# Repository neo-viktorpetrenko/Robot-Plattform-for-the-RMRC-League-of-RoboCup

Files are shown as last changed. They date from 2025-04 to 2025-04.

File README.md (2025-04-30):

# Robot-Plattform-for-the-RMRC-League-of-RoboCup
A Repository for Sharing an easily modifiable and reproducible Robot Plattform including a suspension that was used in the RoboCup German Open 2025 competition

On this Repository a Mechanical Design of a 6 wheeled robot is shared. The robot uses mainly electronic components from EduArt.

cropped

## List of 3D Models
### Models for the front, back and sides of the chassis
|*Amount* | *Component* | *Heatset Inserts M3* | *Multi Filament Print* | *Support Material* | 
| ----- | ----- | ----- | ----- | ----- |
| 1 | Plate Front | 4 | X | X |
|2|Frontlight Cover||✔|X|
|1|Plate Back|4|X|X|
|2|Rearlight Cover||✔|X|
|2|Plate Side A||✔|X|
|1|Plate Side B||✔|X|
|1|Plate Side B with IO Hole||✔|X|

### Models for the floor of the chassis
|*Amount* | *Component* | *Heatset Inserts M3* | *Multi Filament Print* | *Support Material* | 
| ----- | ----- | ----- | ----- | ----- |
|1|Raspberry Pi Bracket||X|X|
|1|Battery Case|4|X|✔|
|1|Plate Bottom A|12 + 4 x M2.5|X|X|
|1|Plate Bottom B|8|X|X|

### Models for the roof of the chassis
|*Amount* | *Component* | *Heatset Inserts M3* | *Multi Filament Print* | *Support Material* | 
| ----- | ----- | ----- | ----- | ----- |
|1|Router Case|4|X|✔|
|1|Plate Top A||X|X|
|1|Plate Top B||X|X|
|1|Plate Top Main Input||X|X|
|1|Camera Servo Holder|4|X|X|
|1|Camera Holder||X|X|

### Models for the suspension
|*Amount* | *Component* | *Heatset Inserts M3* | *Multi Filament Print* | *Support Material* | 
| ----- | ----- | ----- | ----- | ----- |
|4|Suspension Support Center|5|X|X|
|2|Suspension Support Outside|1|X|X|
|6|Suspension Partial Axis|2|X|✔|
|6|Suspension Axis Attachment Plate||X|X|
|3|Suspension Axis Cover||X|X|
|2|Suspension Electronics Cover||X|X|
|3|Motorshield Adapter Plate|2|X|X|
|6|Wheel||✔|✔|

## List of additional components you'll have to buy
| *Amount* | *Component* | *Details* | *Link* |
| ---- | ---- | ---- | ---- |
| 6 | DC Motors | PG25M370 Dc Planetary Gear Motor with Encoder Gear Ratio 64:1 | https://www.nbleisonmotor.com/PG222238-Dc-Planetary-Gear-Motor-pd6514204.html |
| 6 | Torsion Spring | Chosen by calculation, Direction: 90°, used here: Febrotec 0T085-090-422 | https://www.febrotec.de/de-DE/torsionsfedern-schenkelfedern/0t085-090-422/ |
| 1 | Makerbeam Starter Kit |  | https://www.makerbeam.com/makerbeam-makerbeam-regular-starter-kit-black.html |
| 12 | Bearing | Ball Bearing DIN 6002 ZZ 2Z 15x32x9 mm | https://www.conrad.de/de/p/reely-kugellager-radial-chromstahl-innen-durchmesser-15-mm-aussen-durchmesser-32-mm-drehzahl-max-24000-u-min-221954.html |
| 50 cm | Nylon String | diameter 5mm | https://www.conrad.de/de/p/nylonfaden-0-5-mm-100-m-800620811.html |
| 4 | Heat Set Inserts | M2.5x4 | https://www.amazon.de/dp/B09J91JWGM?ref=ppx_yo2ov_dt_b_fed_asin_title&th=1 |
| < 100 | eat Set Inserts | M3x3 | https://www.amazon.de/dp/B09FXNX6WF?ref=ppx_yo2ov_dt_b_fed_asin_title&th=1 |
| 24 | Screws for motors | M2x6 | |
| 4 | Screws for Raspberry Pi 5 | M2.5x10 | |
| 1 | Servo motor for the camera | FT90M Digital Servo  270° Drehwinkel | |
| 6 | Tires | 1:10 RC rubber tires  120 mm outer diameter | https://www.pololu.com/product/1557 |

## Suspension Design
The Suspension of this platform is inspired by the now discontinued Dagu Wild Thumper platform. It uses torsion springs attached to rotating motor enclosures to ensure contact with uneven ground.  Two enclosures on each side are connected with a nylon string to prevent the springs from rotating the enclosures too much.

There are some python scripts in this repository that aid in calculating the behavior of the suspension if you want to modify that. The most relevant dimensions of the suspension are shown in the images below. k in the scripts is the spring constant of the torsion spring. If you order your Springs from Febrotec, you can calculate k = (Max. Torque Md)/(Max. Torsion alpha). For a linear behavior of the suspension, the springs should not be used near the 90-degree rest position. The Most important forces of the calculation are the spring force Ff, the weight Fg and the force acting on a wheel FR.

The Script Suspension_one_curve generates a graph of the force that acts on the wheel at each point in the spring travel xR.
The Script suspension_average_forces generates a grid of the average force within the spring travel for different configurations of l0 and dA1.

CAD2

Zeichnung Drehfeder

Drehfeder rechnung6

grafik

drehfeder rechnung1

grafik

If you don't know the final weight of your modified robot, you can use the excel sheet spring_force_estimation to find out what torsion spring you need. You can set the maximum and minimum weight that your robot will have and change the spring constant to one of a torsion spring you found online. You can use the spring. if the calculated line fits well within the bounds you've set like shown in the graph below.

dimensionierung drehfeder 1

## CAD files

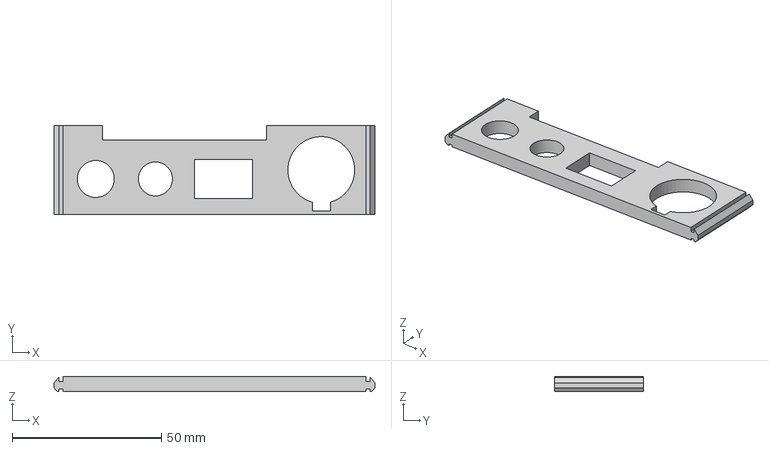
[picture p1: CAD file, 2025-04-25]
Robot Models/Plates/top/Plate Top Main Input/Plate Top Main Input.step
107.6 x 30.0 x 4.89 mm

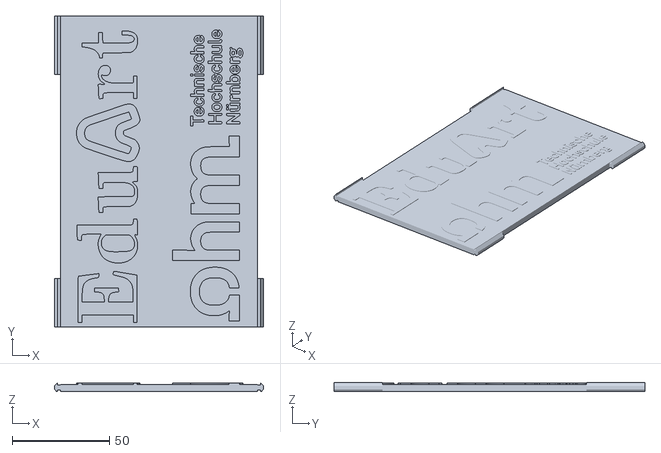
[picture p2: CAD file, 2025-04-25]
Robot Models/Plates/front back sides/Plate Side A/Plate Side A Main Body.stl
107.6 x 160.0 x 4.68

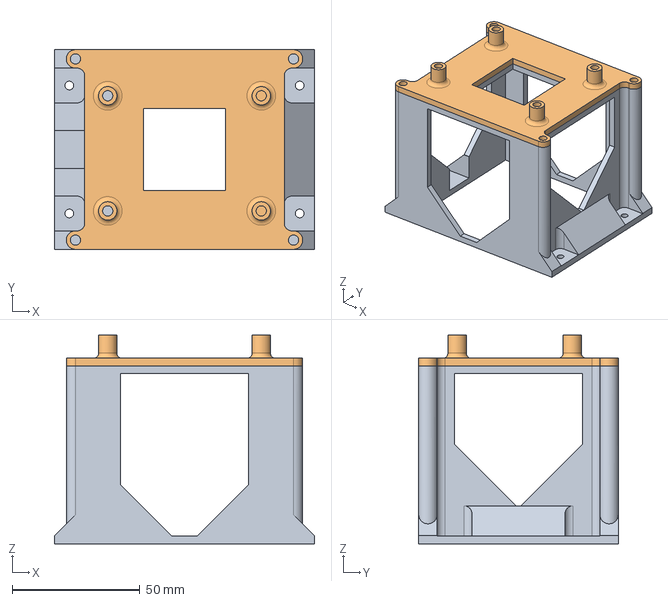
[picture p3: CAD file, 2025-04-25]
Robot Models/Plates/floor/Battery Case/Battery Case.step
101.6 x 78.0 x 81.5 mm

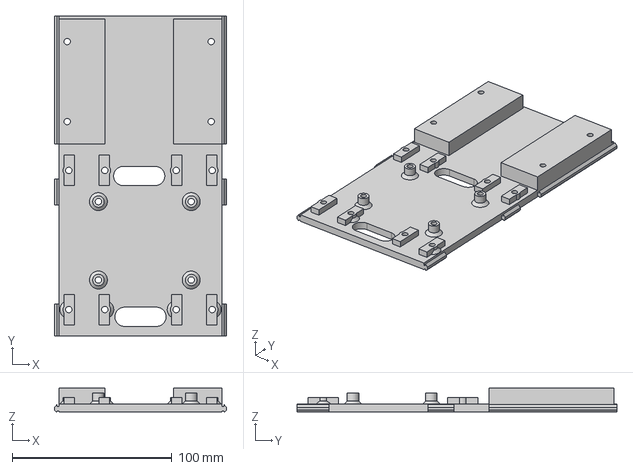
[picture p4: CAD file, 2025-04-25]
Robot Models/Plates/floor/Plate Bottom A/Plate Bottom A.step
107.6 x 200.0 x 14.9 mm

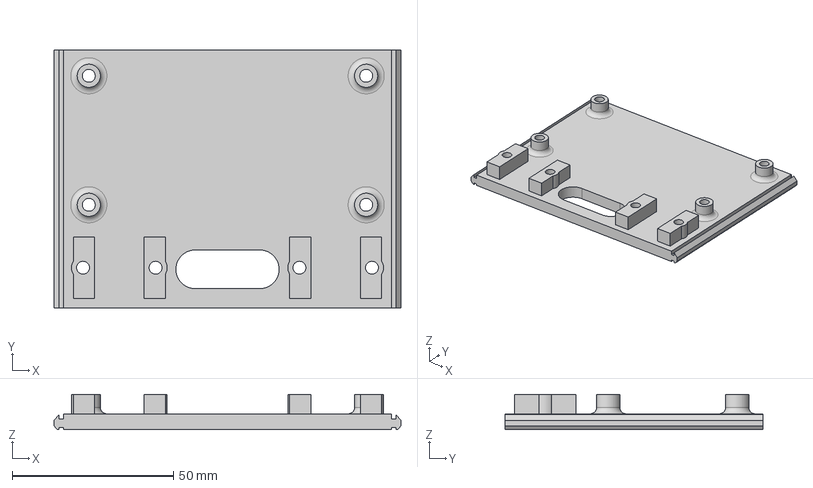
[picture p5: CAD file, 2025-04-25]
Robot Models/Plates/floor/Plate Bottom B/Plate Bottom B.step
107.6 x 80.0 x 10.9 mm

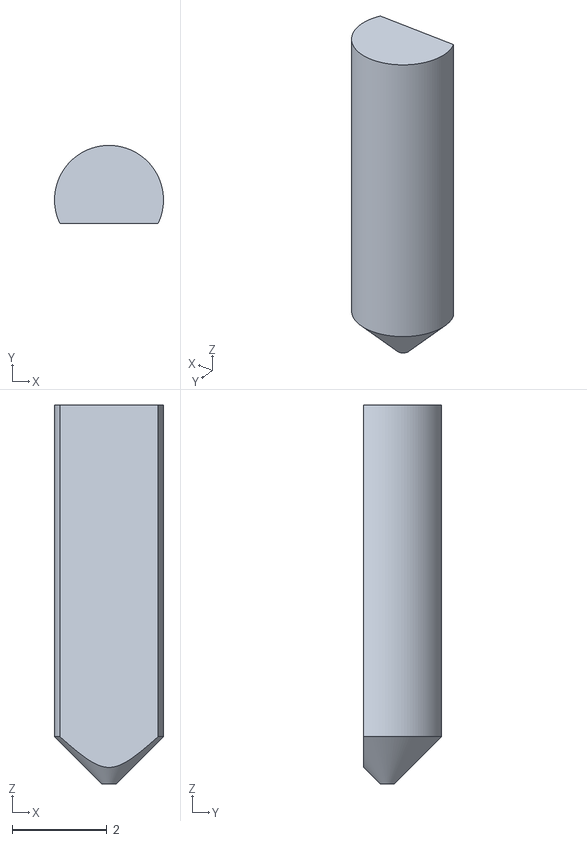
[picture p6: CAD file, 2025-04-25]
Robot Models/Plates/floor/Raspberry PI Bracket/Raspberry PI Bracket pt2.stl
2.30 x 1.65 x 8.00

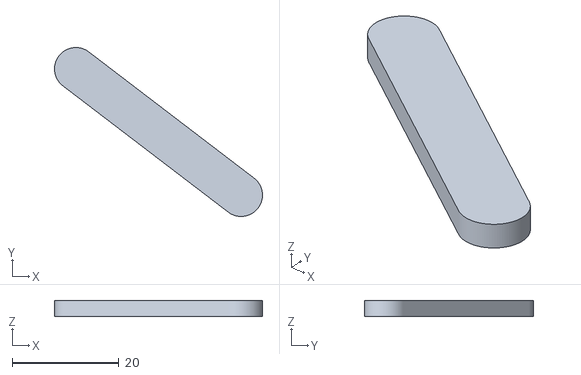
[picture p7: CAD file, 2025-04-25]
Robot Models/Plates/front back sides/Frontlight Cover/Frontlight Cover pt3.stl
39.0 x 31.7 x 3.00

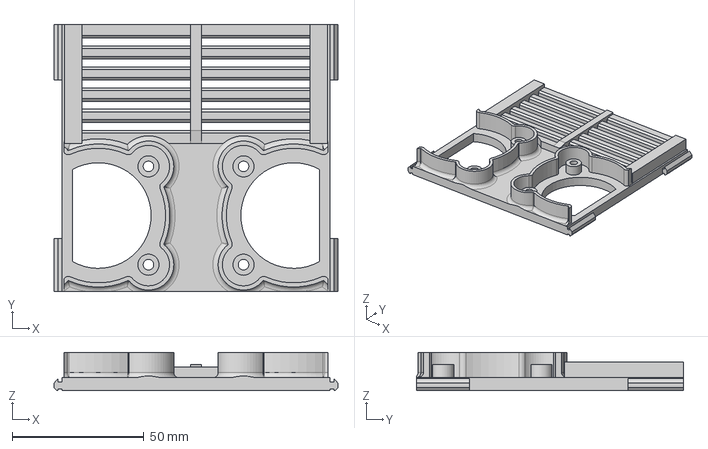
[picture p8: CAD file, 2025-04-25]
Robot Models/Plates/front back sides/Plate Back/Plate Back.step
107.6 x 101.0 x 14.5 mm

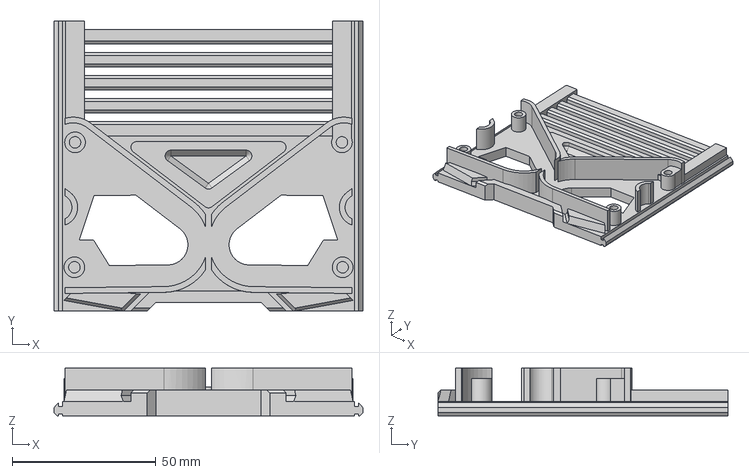
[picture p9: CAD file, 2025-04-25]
Robot Models/Plates/front back sides/Plate Front/Plate Front.step
107.6 x 101.0 x 16.6 mm

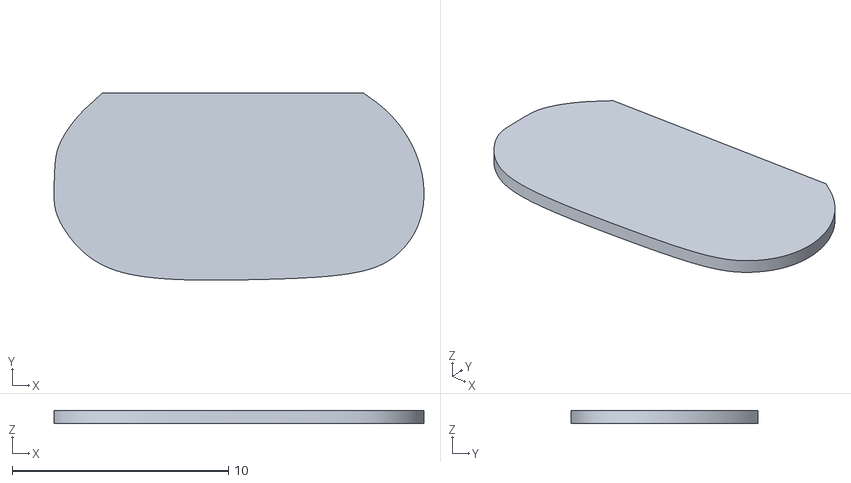
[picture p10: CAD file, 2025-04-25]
Robot Models/Plates/front back sides/Plate Side A/Plate Side A text10.stl
17.1 x 8.67 x 0.6

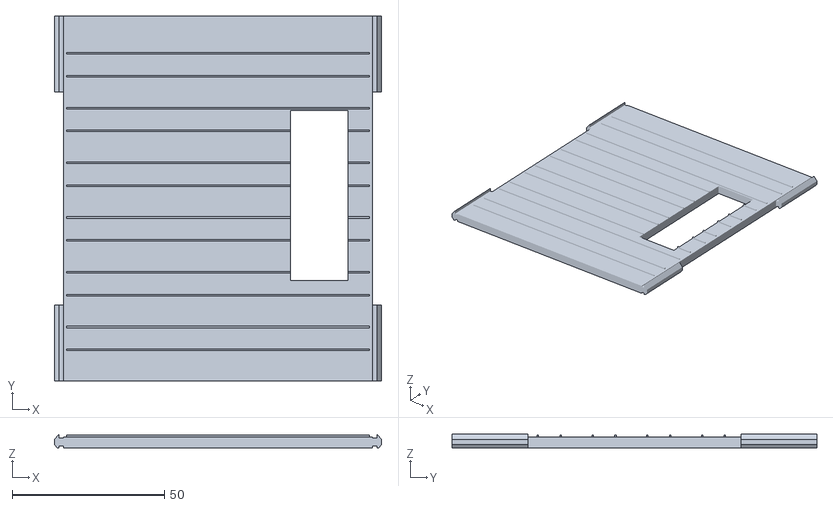
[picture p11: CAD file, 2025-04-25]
Robot Models/Plates/front back sides/Plate Side B with IO Hole/Plate Side B with IO Hole pt1.stl
107.6 x 120.0 x 4.68

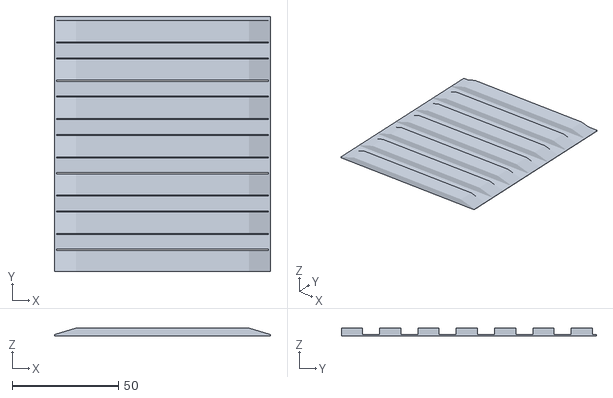
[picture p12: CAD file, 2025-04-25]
Robot Models/Plates/front back sides/Plate Side B/Plate Side B pt2.stl
101.6 x 120.0 x 3.60

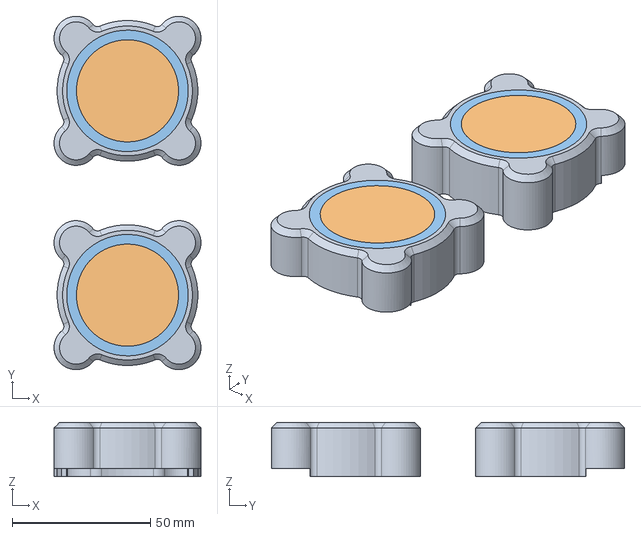
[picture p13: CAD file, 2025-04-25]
Robot Models/Plates/front back sides/Rearlight Cover/Rearlight Cover.step
53.2 x 128.0 x 19.6 mm

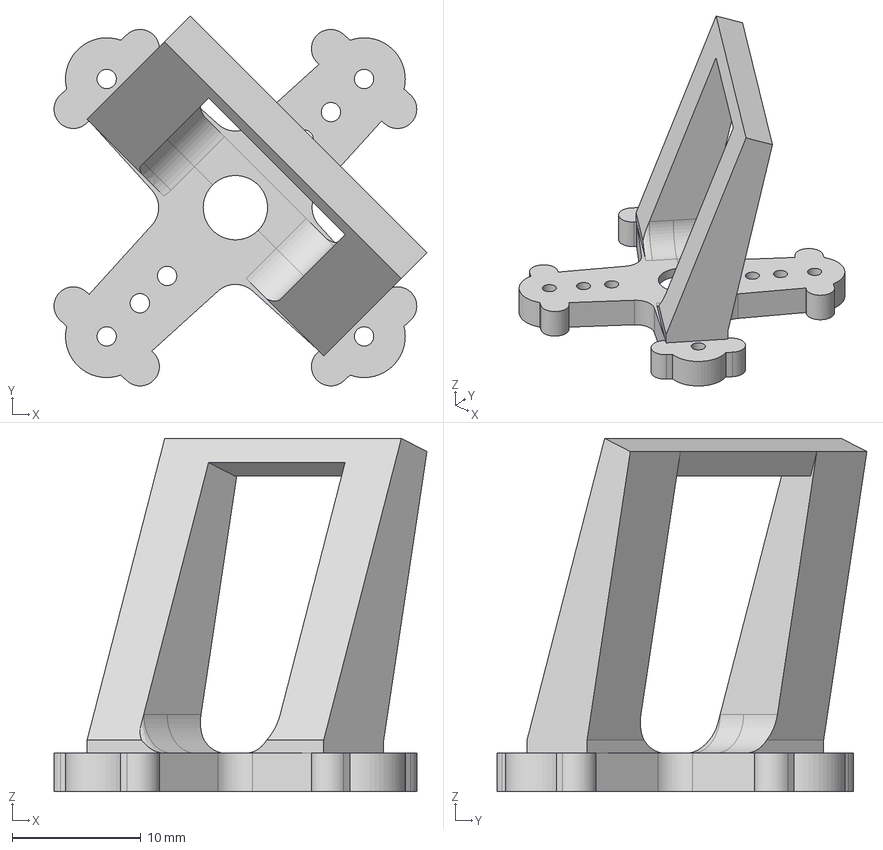
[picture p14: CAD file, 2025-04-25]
Robot Models/Plates/top/Camera Holder/Camera Holder.step
29.0 x 28.7 x 27.4 mm

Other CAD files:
Robot Models/Plates/top/Camera Servo Holder/Camera Servo Holder.step
Robot Models/Plates/top/Plate Top A/Plate Top A.step
Robot Models/Plates/top/Plate Top B/Plate Top B pt2.stl
Robot Models/Plates/top/Router Case/Router Case.step
Robot Models/Plates/floor/Battery Case/Battery Case.f3d
Robot Models/Plates/floor/Battery Case/Battery Case.stl
Robot Models/Plates/floor/Plate Bottom A/Plate Bottom A.f3d
Robot Models/Plates/floor/Plate Bottom A/Plate Bottom A.stl
Robot Models/Plates/floor/Plate Bottom B/Plate Bottom B.f3d
Robot Models/Plates/floor/Plate Bottom B/Plate Bottom B.stl
Robot Models/Plates/floor/Raspberry PI Bracket/Raspberry PI Bracket pt1.stl
Robot Models/Plates/floor/Raspberry PI Bracket/Raspberry PI Bracket pt3.stl
Robot Models/Plates/floor/Raspberry PI Bracket/Raspberry PI Bracket.f3d
Robot Models/Plates/floor/Raspberry PI Bracket/Raspberry PI Bracket.step
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

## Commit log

2025-04-25 Upload Robot Models
    [80 mm alternate wheel pt1.stl, 80 mm alternate wheel pt2.stl, 80 mm alternate wheel.f3d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]
2025-04-30 add calculations
    [spring_force_estimation.xlsx]
